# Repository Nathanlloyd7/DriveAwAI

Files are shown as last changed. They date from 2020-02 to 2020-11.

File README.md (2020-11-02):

# DriveAwAI - Final Year Project - Nathan Lloyd
Welcome to my Final Year Project as an undergraduate, the aim of this project is to have a semi autonomous vehicle that naturally has the ability to toggle between assisted. This will be done utilising a Pi 4, Coral TPU and explorerHAT Pro.

## Objectives
* Create a Raspberry Pi RC Car
* Provide a suitable GUI control
* Include autonomous driving elements, utilising computer vision
* Provide suitable security 

## Shopping List

Item | COST | Link
-----|------|-----
Raspberry Pi 4 | £30 - 50 | https://thepihut.com/products/raspberry-pi-4-model-b?variant=20064052740158
SD Card (Recommend 32GG+) | ?? | UP2U
ExplorerHat Pro | £20 | https://thepihut.com/products/explorer-hat
Coral TPU | £75| https://www.mouser.co.uk/ProductDetail/Coral/G950-01456-01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
PiCam V2 | £25 | https://thepihut.com/products/raspberry-pi-camera-module
PiCam Mount | £3 | https://shop.pimoroni.com/products/raspberry-pi-camera-mount
Extra Webcam | £? | https://www.amazon.co.uk/TeckNet%C2%AE-1080P-Webcam-Built-Microphone/dp/B003VOEENG
Motors & Wheels | £8 | 2 PCS DC Gear Motor + Tire Wheel for Arduino DC 3V-6V
Fan Shim | £10 | https://thepihut.com/products/fan-shim-for-raspberry-pi
Ninja Case | £8.50 | https://thepihut.com/products/pibow-4-coupe-case-for-raspberry-pi-4b?variant=20452597661758  
Dragging Wheel (Shooping Cart) | £3 | https://www.amazon.co.uk/gp/product/B007OXBMQM/ref=ppx_yo_dt_b_asin_title_o00_s00?ie=UTF8&psc=1
Jumper Wires M-M | £5 | https://www.amazon.co.uk/gp/product/B0144HG2RE/ref=ppx_yo_dt_b_asin_title_o01_s00?ie=UTF8&psc=1
LED's x2 | £2.50 | https://thepihut.com/products/adafruit-diffused-5mm-led-pack-5-leds-each-in-5-colors-25-pack-ada4203
Resistor x2 | £6 | https://thepihut.com/products/ultimate-resistor-kit
Blue Tape | £1 | https://www.amazon.co.uk/gp/product/B0001IXA76/ref=ppx_yo_dt_b_asin_title_o02_s00?ie=UTF8&psc=1
Pi Cam Ribbon Ext | £4 | https://www.amazon.co.uk/gp/product/B01MU2HAOM/ref=ppx_yo_dt_b_asin_title_o03_s00?ie=UTF8&psc=1
Toy Traffic Signs | £12 | https://www.amazon.co.uk/gp/product/B07PD2M9C4/ref=ppx_yo_dt_b_asin_title_o00_s00?ie=UTF8&psc=1
Battery Pack | TBD | TBD
Webcam  up2u | up2u
Total| £200 -£250 | I've not gone out to look for the best deal, so please do that yourself.

Some of the above aren't exactly what I bought and in some cases I had parts laying around from previous projects. This is just a guide to what you may need if you fully recreate. 

## Car Body
I have had a lot of help from a friend designing a chassis to fit the items I've accumilated, you can use whatever you want for your body... but the CAD models and designs will be displayed within a folder shortly.

## Extra Camera
As noted in my 2nd report, an Issue was running the Object detection model as well as onboard camera display using the same input. A simple workaround was using two cameras and mounting the second on top.

## Installing Coral TPU
Step 1: Install Coral TPU - https://coral.ai/docs/accelerator/get-started/

>echo "deb https://packages.cloud.google.com/apt coral-edgetpu-stable main" | sudo tee /etc/apt/sources.list.d/coral-edgetpu.list
>curl https://packages.cloud.google.com/apt/doc/apt-key.gpg | sudo apt-key add -
>sudo apt-get update

>sudo apt-get install libedgetpu1-std

Step 2: Install TF for Python - https://www.tensorflow.org/lite/guide/python
>pip3 install https://dl.google.com/coral/python/tflite_runtime-2.1.0.post1-cp37-cp37m-linux_armv7l.whl

Step 3: Check Installs by running a model
>mkdir coral && cd coral
>git clone https://github.com/google-coral/tflite.git

>cd tflite/python/examples/classification
>bash install_requirements.sh

>python3 classify_image.py \
>--model models/mobilenet_v2_1.0_224_inat_bird_quant_edgetpu.tflite \
>--labels models/inat_bird_labels.txt \
>--input images/parrot.jpg

# Installing Requirements
Step 1: <br/>
>Enable i2c, SSH, Camera and VNC  in Raspberry Pi config.<br/>

Step 2:<br/>
>Download the project if you haven't already.<br/>

Step 3:<br/>
>Unzip<br/>

Step 4:<br/>
>Navigate to the directory (/DriveAwAI-Nathanlloyd7) through terminal, here you can find the requirements doc. Then Run <br/>
>pip install --user --requirement Requirements.txt<br/>

Step 5: <br/>
>Run main: default password on SenseHat PIN password = 4321. Have fun with your new car

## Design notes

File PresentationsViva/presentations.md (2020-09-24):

# Why?
*I have decided to upload my viva presentations for safekeeping as access to the onedrive has been removed upon graduating.*

**Click Images to go to video**

## Video 1
* The problem
* The chassis
* The GUI

Video 1 (https://youtu.be/bGszfEqLIKk "Video 1 - Click to Watch!")

## Video 2
* Project Management, Issues & Flexibility 
* PIN Sytem Security
* Hashing PIN Password

Video 2 (https://youtu.be/l-lXbyoH-wU "Video 2 - Click to Watch!")

## Video 3
* Coral TPU
* What problem to tackle?
* The dataset & Transfer learning
* New Data & Processing
* Methodology 
* TensorFlow & Google Cloud
* TensorBoard
* Model analysis
* Implementation
* Future Improvements

Video 3 (https://youtu.be/PnvW7pgBxbs "Video 3 - Click to Watch!")

## Video 4
* Device Walkthrough

Video 4 (https://youtu.be/6IMir6JdNHE "Video 4 - Click to Watch!")

## Video 5
* Github
* Project Management Stategies
* Problems faced

Video 5 (https://youtu.be/kdOTbvWSUvU "Video 5 - Click to Watch!")

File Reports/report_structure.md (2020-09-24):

# Reports

*My dissertation project report is split into two segments due to the assessment structure.* 

## Part 1 
* Literature review
* Systems design and technical documentation
* The test plan 
* Current development timeline

## Part 2 
* Additional literature review discussing problems and objectives
* Development lifecycle
* Implemented and finished designs
* Core features
* Model development
* Model analysis 
* Critical analysis of tools and practices.

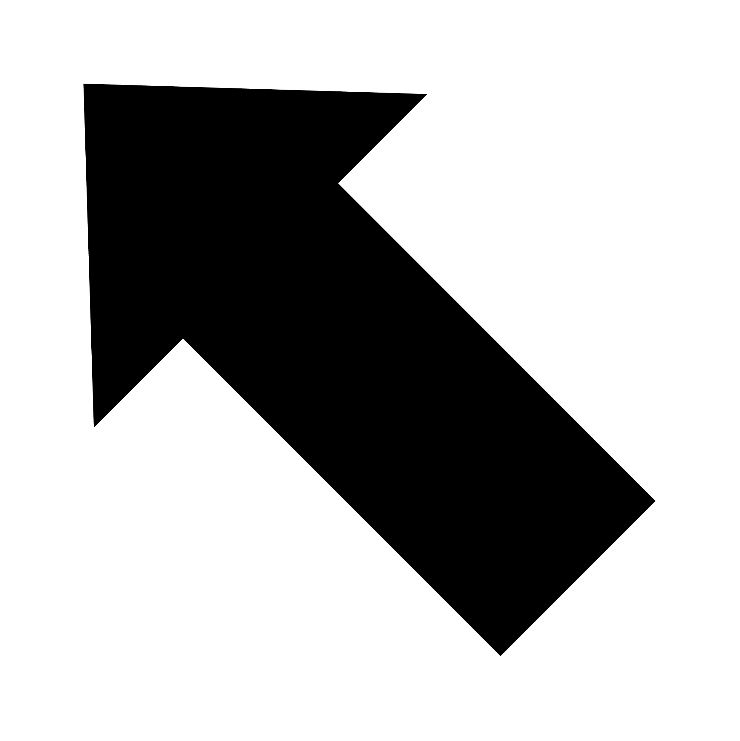
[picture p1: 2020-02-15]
Code/Images/Arrow-UL.png

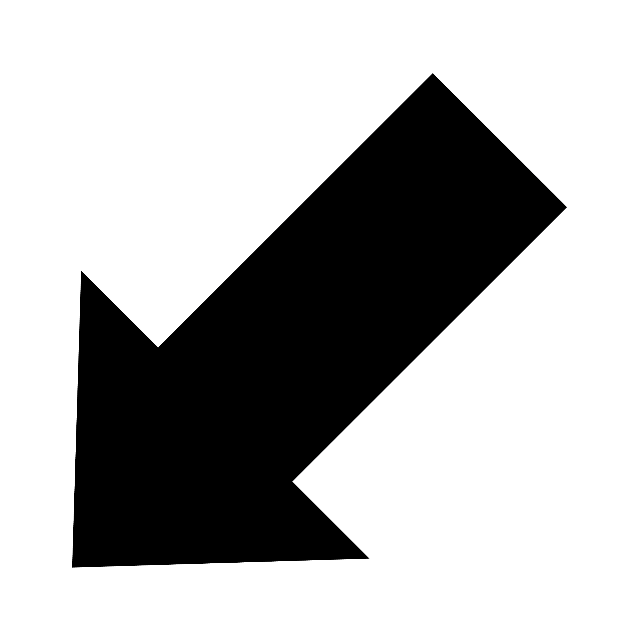
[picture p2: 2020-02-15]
Code/Images/Arrow-DL.png

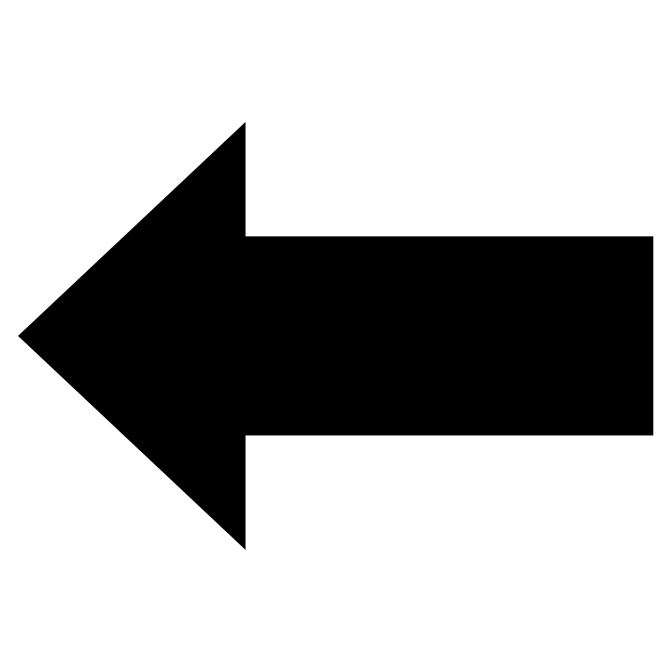
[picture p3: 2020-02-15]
Code/Images/Arrow-LE.png

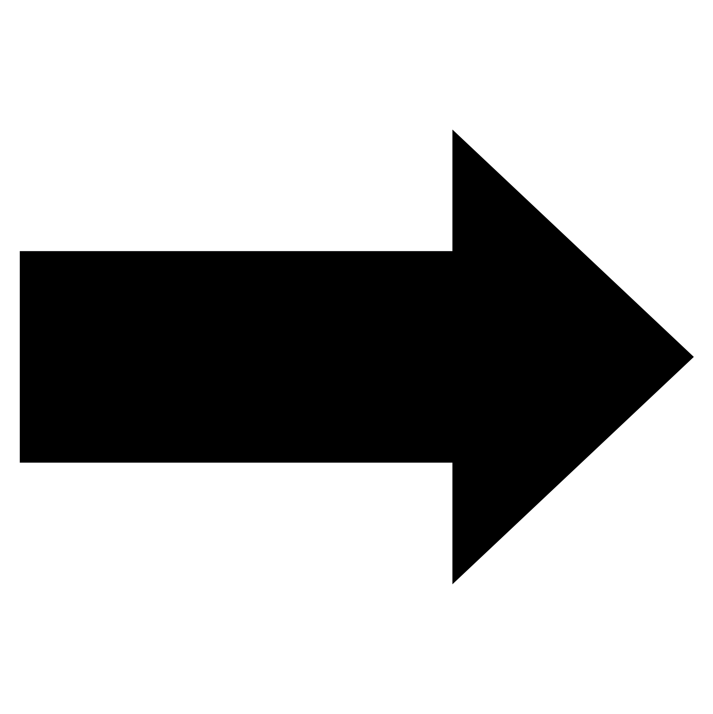
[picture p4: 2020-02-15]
Code/Images/Arrow-RI.png

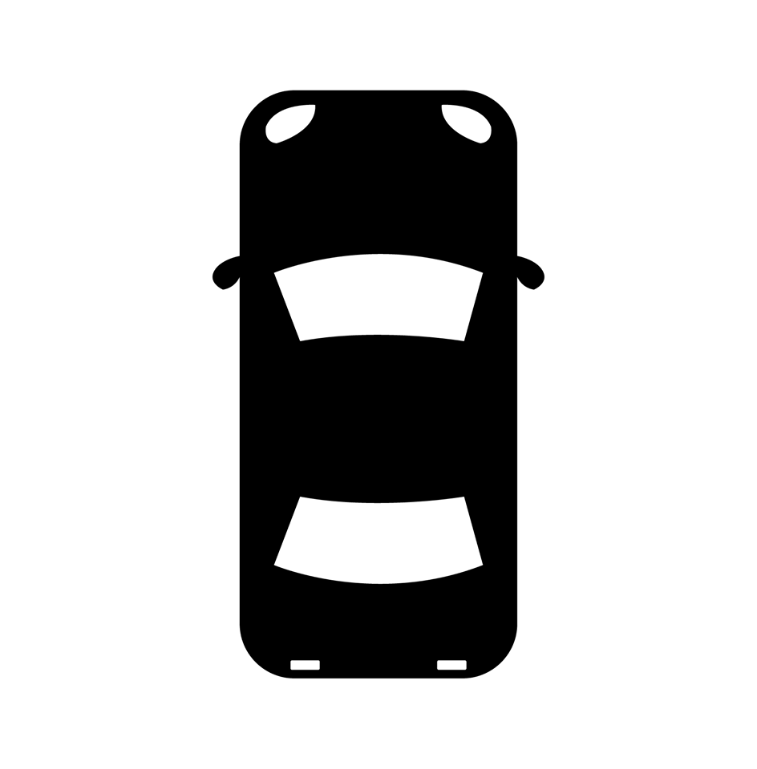
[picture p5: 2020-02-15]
Code/Images/realcar1.png

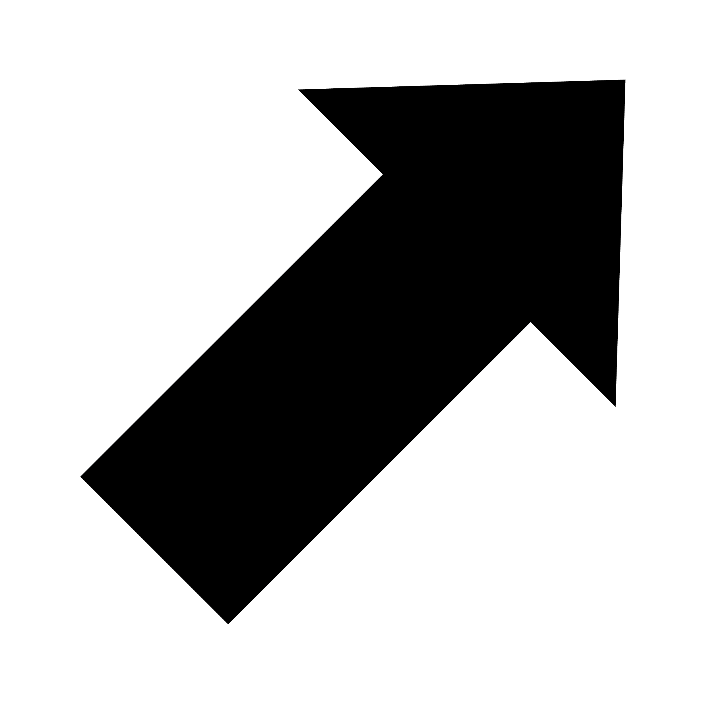
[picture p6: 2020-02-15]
Code/Images/Arrow-UR.png

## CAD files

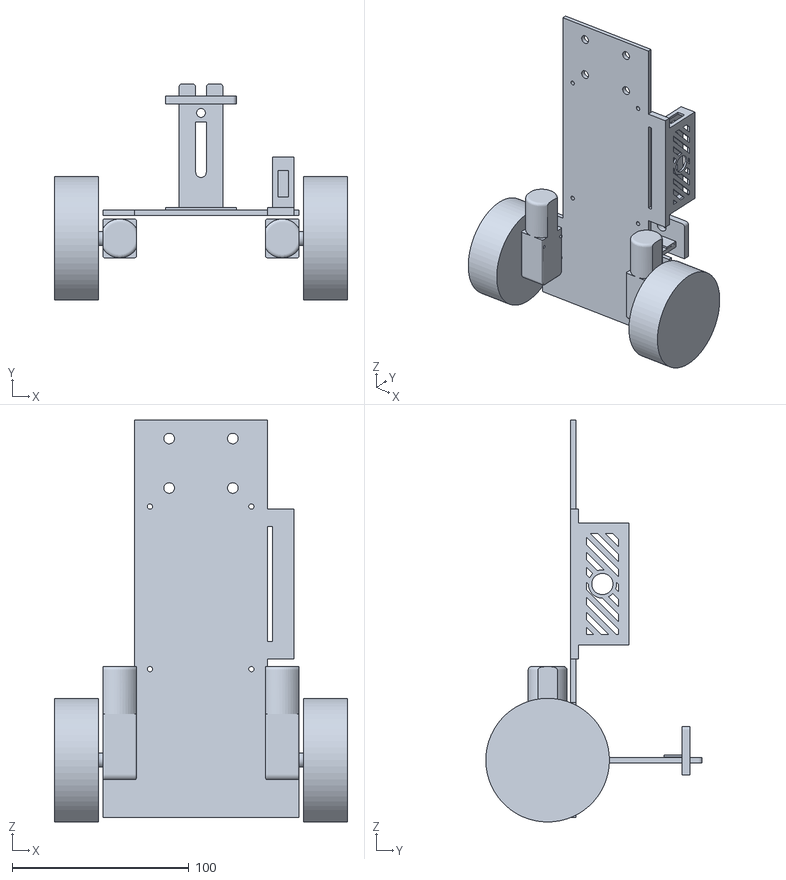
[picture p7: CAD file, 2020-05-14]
3D-Designs/FullModelWithoutMotorCasings.STL
166.0 x 122.5 x 227.5

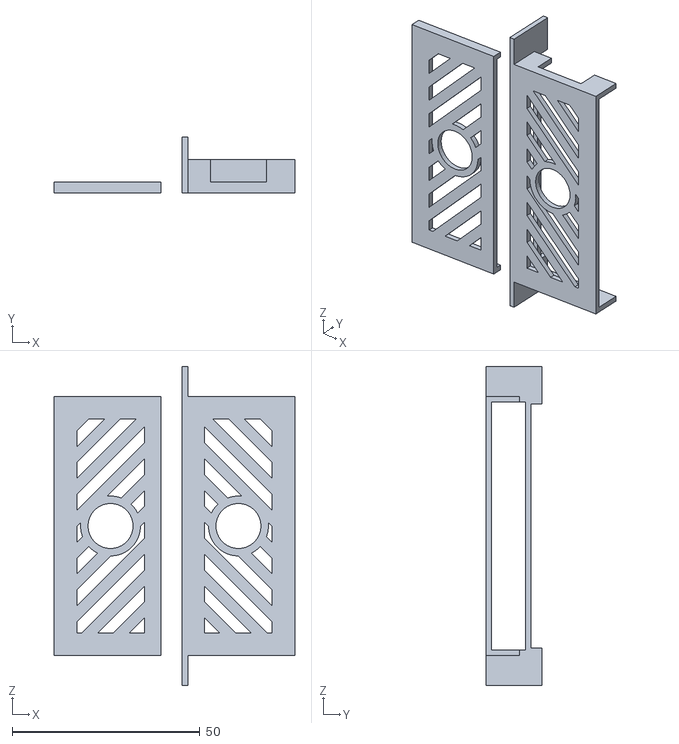
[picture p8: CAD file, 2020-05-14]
3D-Designs/CoralCase.STL
64.1 x 15.0 x 85.0

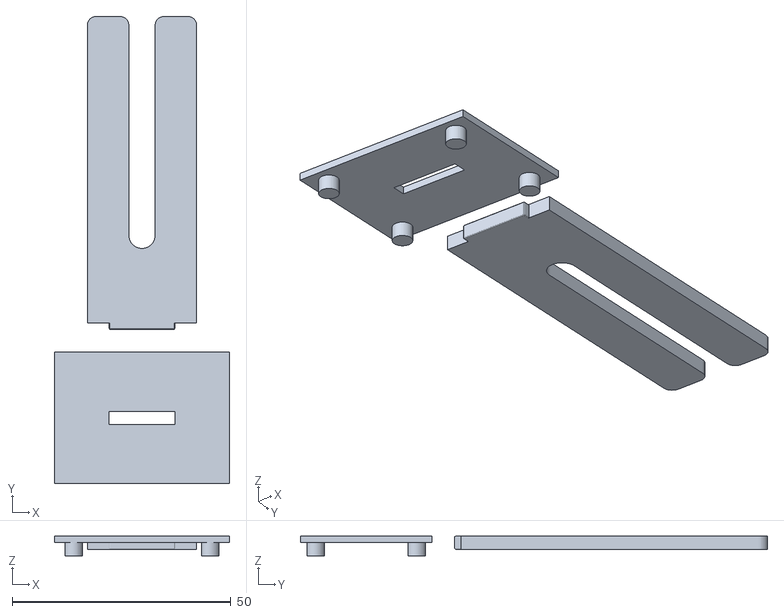
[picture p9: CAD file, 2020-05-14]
3D-Designs/CameraStand.STL
40.0 x 106.7 x 4.50

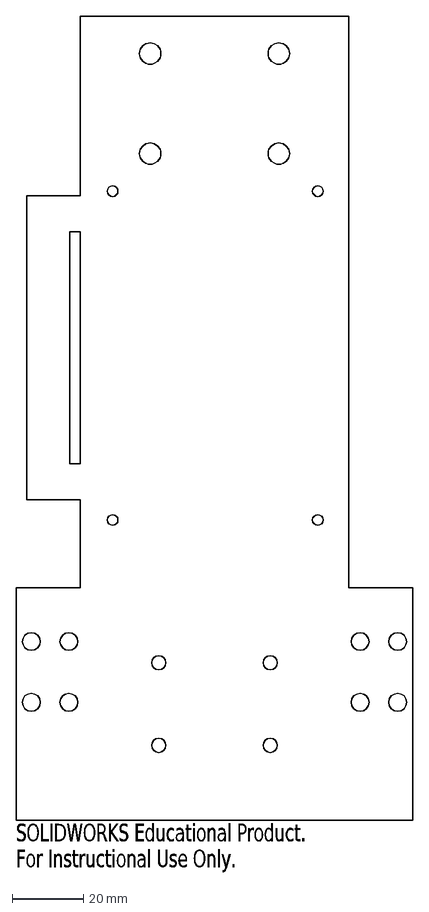
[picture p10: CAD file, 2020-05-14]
3D-Designs/BaseTemplateLaserCutting.DXF
SOLIDWORKS Educational Product.
For Instructional Use Only.

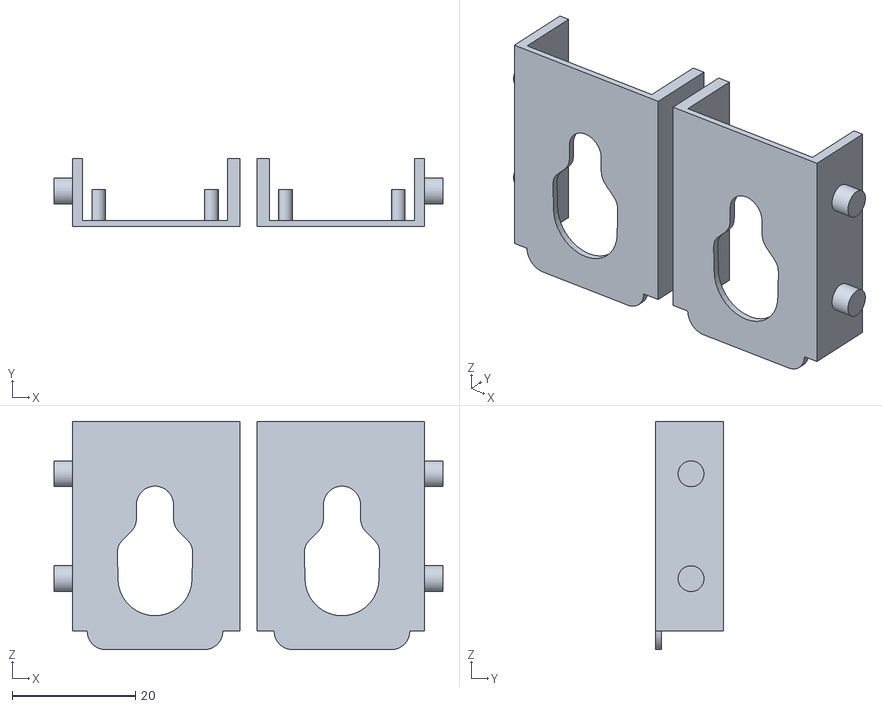
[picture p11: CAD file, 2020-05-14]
3D-Designs/MotorCasing.STL
63.0 x 11.0 x 37.0

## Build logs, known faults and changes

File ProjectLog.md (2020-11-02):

# DriveAwAI
Final Year Project

This is my dissertation project to create a rc car and develop it to have some level of automation using images. This will be used as a log/update for myself.

03.09.19
[Added in after the fact]
Assembled electronics and did some research into the cassis of the Pi car, looked into accelerators for increased calculation speed. Built some basic functions to do directions etc. Soldered wires to motors.

08.09.19
Building on previous basic motor control I've been working on some basic GUI's using tkinter. I've created three column panels: speed, directiom, video view. The latter of which is just a default panel seen on a tutorial, currently they do not interact with the motors as I ran out of time and couldn't upgrade to an RCCar Class. Future updates will include this, at the moment the buttons will just print their expected future feature. This is a very simple draft of the panels, more items may be added in future.
In the meantime of creating the gui and learning some basic tkinter I have started the fast.ai course which library sits on top of pytorch, this looks like a very efficient way of implementing ML. And with a coral TPU accelerator I think the overall goal will be very achievable.

12.09.19
Been busy over the last few days, not much programming or research taken place. I have put a few minutes in here and there to fix problems I was stuck on last week. I can now call methods when clicking a button which is the first GUI interaction I've achieved between motor and gui. I've also been pseduo coding a rc car class, and have put together a simple set motor implementation and it works fine, will just need to fit it with actual code and test it over the gui over the coming days. Done a little quote hunting collection and put them together for my lit review too. 
--Ext: After spending time of making a functional RC class, I've hit the problem I thought I may have by putting my speed and distance into seperate containers. when speed is updated, the direction panel has no idea. For this to be solved, do I simply need to use global variables or should I make new methods that send this info over? 

!!I think the best way forward would be to initialize my rc car in the RCTK window and have all my panels speak to this window.

19.09.19
Moved into Uni halls now, so potentially more frequent work. Merged the speed and direction panel into a movement panel. Adding diagonal turning too, currently the buttons don't match up in size, but eventually I will use images(arrows) to point in the direction. DIrections have not been coded in other than forward and backward as there is no chassis, so right and left is undecided. Added in a scale/slider for speed as it is more representative of real driving. Also added some basic menu buttons. Need to clean the code out and ideall would like to OOP up my menu buttons to make RCTK cleaner. But it is less important as these are secondary features. Still trying to find out how to access a stream of the picam too. Have some ideas but not seen any absolutes as of yet.

23.09.19
Added minor features to some of the menu items and changed about from a new window to a message box. I can see these menu items taking up a lot of room and it's not too clean coding having them in the RCTK file. Might need to implement OOP in the future to bring these menu items in. However I might save cleaning up my code until I have working up features as it is more important I get things working first.

27.09.19
Swapped to a pair of radio buttons for my one menu item. the menu saves and loads as expected but I can't display in the log box. I can sometimes get one working but not the other, could be an issue with the var or the r+/w+ access.

01.10.19
Created a new menu class to clean up RCTKWindow, I broke the save and load feature because of it but very happy with the cleaner approach. This approach as I followed a stack overflow posting meant I had to drop my root naming convention in RCTK in favour of initialising by tk.TK__init__(self) but other than those two issues fairly simple. Would be nice if I could get controller settings for a future update. Also realised I haven't posted the widget icon 'realcar1.png' but fairly straight forward so I wont post. Really happy with progress so far, think I'm going to go down an opencv & Tensor flow route so I can have an opencv stream in tkinter whereas currently getting the video in a frame is out of my knowledge.

04.10.19
Only small change today, got the save and load features working for the radio buttons on motor settings. Not as clean as I would like but it gets the job done. Next stage will be getting the loaded variables for the menu to actually interact with the panels

13.10.19
Videopanel added in, opencv needed for videostream as there is some complications when threading rpicam. Had a majority of the code done a few days ago but got stuck due to unfamiliarity with open cv syntax. Tried to use params where they weren't needed, but it is fixed now and working. Might look to add a menu that changes view by an open cv filter. "Night vision" Etc. Also looking to add "security features" where I can make use of the touch sensors on the explorer hat and make a password system.

16.10.19
Ran images for buttons through PhotoImage and they were too big and so couldn't resize, now using PIL library to edit them in app. Using images for buttons has slowed the start up slightly. Optimising this would be ideal. Changed the layout of code for rc and menu, initialising them both as self will allow me to use more features and have cleaner code.
----- I am definately keen on this password idea as well as some fun features like a horn.

21.10.19
Gone home for the week and so I haven't done any coding or research as I want some downtime, I have started to fill in a project contract however and decided to go from a scientific title to a more commerical one. I have decided to give the project an official name of 'Drive AwAI' which stands for "Drive Assisted with AI", I really like the title name and have enjoyed the downtime. I am looking forward to carrying on with the work at the end of this week. Hopefully I can add in a few fun features, the University has purchased a coral TPU on my behalf which is great. As I am already ahead of schedule, getting this device puts me even further ahead as it is the device I had in mind at the start of the project and now I do not need to replan or pay extra money to ensure I get it operational.

26.10.19
Quick little security password for my RC, thought I might as well use the touch sensors on the explorerhat as they make a great PIN entry system. Found a majority of this programming online but added the ability to change the password, next step will be saving and loading a password in. Might add it into my settings folder but I'm not sure how without deleting other settings. Works fine, just need to clean up the looping system and find out how to attach to the rest of the app, it is low priority at the moment though. Got the Coral TPU this week too, so I can start earlier than planned on ML.

10.11.19
With other deadlines looming way before this one, and already being a decent way through the development of the front end of this app I've taken my foot off the gas and will continue to do so for another week I expect. I have been making a list and updating my development timeline accordingly though. I did get a bit bored though and wanted to get the password system in place, I've made the password load in from a txt file called, passSeting.txt, and then split the string and cast so they can be formatted into a list. This means I can simply enter a string when I edit the change password setting and not have any complicated stuff. I did try and get the TPU on, but as I already had a previous install of tf and a workaround method for 3.5 python. It would seem as they now support 3.7 there is a clash, will have to uninstall libraries or reformat the SD and reinstall from scratch.

15.02.20
Long time since the last log, bogged down with other uni work but I have been working on this as some commits show. I have a model working with the TPU but it currently doesn't effect the Pi, it can see but not act upon anything. I have also been working on the chassis and its nearly complete. Because of this I can add directional functionality... however, it may need fine tuning. I have spent some of the day just cleaning up the files, I want be able to curl in my files between different SD cards and have everything pre-installed by doing so. So a bit of housekeeping is going to occur to do this.

17.02.20
Have created requirements file.
Have also added extra security by hashing the pin passwords.**Hash of these commits matches 4321, however, github adds whitespace at the end of the line, so please remove this**

03.03.20
Removed flip from the video stream. 
Spent the last week finishing up the core driving elements, motors are now installed using 3D printed elements, car can now be driven using GUI. Need to shift the minimum speed selectable though in slider. 35 is too slow. 50 is new minimum.

Also bought toy model traffic signs, taken 120 photos containing around 250 object instances. Used LabelImg to box the signs and toy person. Got a few left to do as I need to retake a few photos due to poor image quality. After this I can xml -> CSV -> TFRecord ... and then start training (transfer learning on MobileNet v2 SSD COCO), COCO contains a few objects that I could use anyway, such as cars, people, trucks et. MobileNet v2 SSD is well documented and middleground of accuracy and speed. May try and train my own from scratch not using COCO but will see.

11.05.20
It has been a very long time since I have used the log. I will give a very short but sweet update on what I've been working on.
- Chassis is virtually done
- There are loads more photos and objects within each photo
- Three models were created, expanding dataset each time
- 3rd Model, although could be improved further is suitable
- Coral TPU is a pain to work with 'libedgetpu.so.1' is the bain of my existence
- I can get the model to work outside of the application and control motors seperately
- GUI barebones is done.

Project is nearly at the end for what I set out to do. I have a week left to try and wrestle the edgetpu into submission, otherwise I have a tech demo for the model controlling motors and a seperate one for the GUI/Security/Car. Bit of a pain to have everything done but the last segments not wanting to co-operate.

02.11.20
Bit late on the total project update, I graduated CompSci with a first and got 98% in my dissertation project overall. Managed to wrangle the last bit of the project together and everything worked as expected in the end; see my presentations and reports that were uploaded previously. I am just revisting this project now as I wanted to have a bit of closure on the last whitespace "feature" of the hashed password (all it took was an rstrip). Overall this has been a very fun project and has introduced me to loads of cool AI/Deep Learning content. I'm continuing my studies in a masters, hopefully upskilling from implementing others NN's in transfer learning to making my own from scatch :D.

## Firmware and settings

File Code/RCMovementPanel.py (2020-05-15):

#control direction of rc
from tkinter import *
from Code.RCCar import *
from PIL import Image, ImageTk
import os
import Code.RCAutomated as rcauto


class RCMovementPanel:
    def __init__(self, root, frame):
        self.rc = RCCar(True, 50, 50)
        self.root = root
        self.frame = frame
        dlpath = os.getcwd()
        motorSetsFile = open(dlpath+"/Code/Settings/motorSetting.txt", "r") #current setup lets you save to a doc but not show in a log or print in??
        global loadedVar
        loadedVar = motorSetsFile.read(1)
        
            
            
        
        
        
#images import and process into smaller size
        try:
            self.arrowSy = 50   #customizable maybe a menu item?
            self.arrowSx = 50
            self.arrowUp = Image.open(dlpath+"/Code/Images/Arrow-UP.png")
            self.arrowUp = self.arrowUp.resize((self.arrowSx,self.arrowSy), Image.ANTIALIAS)
            self.arrowUp = ImageTk.PhotoImage(self.arrowUp)

            self.arrowUr = Image.open(dlpath+"/Code/Images/Arrow-UR.png")
            self.arrowUr = self.arrowUr.resize((self.arrowSx,self.arrowSy), Image.ANTIALIAS)
            self.arrowUr = ImageTk.PhotoImage(self.arrowUr)

            self.arrowUl = Image.open(dlpath+"/Code/Images/Arrow-UL.png")
            self.arrowUl = self.arrowUl.resize((self.arrowSx,self.arrowSy), Image.ANTIALIAS)
            self.arrowUl = ImageTk.PhotoImage(self.arrowUl)

            self.arrowRi = Image.open(dlpath+"/Code/Images/Arrow-RI.png")
            self.arrowRi = self.arrowRi.resize((self.arrowSx,self.arrowSy), Image.ANTIALIAS)
            self.arrowRi = ImageTk.PhotoImage(self.arrowRi)

            self.arrowLe = Image.open(dlpath+"/Code/Images/Arrow-LE.png")
            self.arrowLe = self.arrowLe.resize((self.arrowSx,self.arrowSy), Image.ANTIALIAS)
            self.arrowLe = ImageTk.PhotoImage(self.arrowLe)

            self.arrowDl = Image.open(dlpath+"/Code/Images/Arrow-DL.png")
            self.arrowDl = self.arrowDl.resize((self.arrowSx,self.arrowSy), Image.ANTIALIAS)
            self.arrowDl = ImageTk.PhotoImage(self.arrowDl)

            self.arrowDo = Image.open(dlpath+"/Code/Images/Arrow-DO.png")
            self.arrowDo = self.arrowDo.resize((self.arrowSx,self.arrowSy), Image.ANTIALIAS)
            self.arrowDo = ImageTk.PhotoImage(self.arrowDo)

            self.arrowDr = Image.open(dlpath+"/Code/Images/Arrow-DR.png")
            self.arrowDr = self.arrowDr.resize((self.arrowSx,self.arrowSy), Image.ANTIALIAS)
            self.arrowDr = ImageTk.PhotoImage(self.arrowDr)

        except:
            print("Something went wrong, File not found")




#Frame for Directional Buttons & speed
        Label(self.frame, text="Direction:").grid(row=0, column=0, padx=10, pady=2)

#top row
        self.topFrame = Frame(self.frame, width=200, height=10, borderwidth=1)
        self.topFrame.grid(row=1, column=0, padx=10, pady=2)
        self.left_upBtn = Button(self.topFrame, text="diag", image=self.arrowUl, command= self.rc.goUpLeft)
        self.left_upBtn.grid(row=1, column=1, padx=10, pady=2)
        self.upBtn = Button(self.topFrame, text="Up",image=self.arrowUp, command= self.rc.goForward)
        self.upBtn.grid(row=1, column=2, padx=10, pady=2)
        self.right_upBtn = Button(self.topFrame, text="diag", image= self.arrowUr, command= self.rc.goUpRight)
        self.right_upBtn.grid(row=1, column=3, padx=10, pady=2)
#Frame to Hold left, stop and right
        self.midFrame = Frame(self.frame, width=200, height=10, borderwidth=1)
        self.midFrame.grid(row=2, column=0, padx=10, pady=2)
        self.leftBtn = Button(self.midFrame, text="Left",image = self.arrowLe, command=self.rc.goLeft)
        self.leftBtn.grid(row=0, column=0, padx=10, pady=2)
        self.stopBtn = Button(self.midFrame, text="Stop", command = self.rc.handbreak)
        self.stopBtn.grid(row=0, column=1, padx=10, pady=2)
        self.rightBtn = Button(self.midFrame, text="Right",image = self.arrowRi, command =self.rc.goRight)
        self.rightBtn.grid(row=0, column=2, padx=10, pady=2)
#Down
        self.botFrame = Frame(self.frame, width=200, height=10, borderwidth=1)
        self.botFrame.grid(row=3, column=0, padx=10, pady=2)
        self.left_downBtn = Button(self.botFrame, text="Diag",image=self.arrowDl, command= self.rc.goBackLeft)
        self.left_downBtn.grid(row=0, column=1, padx=10, pady=2)
        self.downBtn = Button(self.botFrame, text="Down",image=self.arrowDo, command= self.rc.goBack)
        self.downBtn.grid(row=0, column=2, padx=10, pady=2)
        self.right_downBtn = Button(self.botFrame, text="Diag", image=self.arrowDr,command= self.rc.goBackRight)
        self.right_downBtn.grid(row=0, column=3, padx=10, pady=2)
        Label(self.frame, text=" ").grid(row=4, column=0, padx=10, pady=2)
#Auto/Man Toggle
        
        self.aiTogBtn = Button(self.frame, text="Ai Toggle", command=rcauto.goAI)
        self.aiTogBtn.grid(row=5, column=0, padx=10, pady=2)
#speed
        global scale
        Label(self.frame, text=" ").grid(row=6, column=0, padx=10, pady=2)
        self.speedFrame = Frame(self.frame, width=200, height=10, borderwidth=1)
        self.speedFrame.grid(row=7, column=0, padx=10, pady=2)
        Label(self.speedFrame, text="Speed:").grid(row=0, column=0, padx=10, pady=2)
        self.scale = Scale(self.speedFrame, from_ = 35, to = 100, orient = HORIZONTAL)
        self.scale.grid(row=1, column=0, padx=10, pady=2)
        self.scale.set(75)                                                                           #sets default speed
        self.setSpeed = Button(self.speedFrame, text="Set Speed", command = self.returnSpeed)
        self.setSpeed.grid(row=2, column =0, padx=10, pady=2)
            
    def returnSpeed(self):
        if int(loadedVar) == 1:
            self.rc.set__spd(self.scale.get())
            print (self.scale.get())     #mock function for now
        elif int(loadedVar) == 0:
            messagebox.showwarning(title="Modification = Off", message = "This safety feature has been toggled.\nPlease go to Motor settings to remedy this!")
            print("control off")
        else:
            print('An error occurred trying to analyse file contents')
     
       
    def speedOff(self):
           setSpeed.configure(state="disabled")
           scale.config(state=DISABLED)
           

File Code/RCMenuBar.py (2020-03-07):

import tkinter as tk
from tkinter import *
from tkinter import messagebox
import sys
import os

class RCMenuBar(tk.Menu):
    def __init__(self, parent):
        tk.Menu.__init__(self, parent)
        dlpath = os.getcwd()
        fileMenu = tk.Menu(self, tearoff=0)
        self.add_cascade(label="File",underline=0, menu=fileMenu)
        fileMenu.add_command(label="Control Settings",underline=0, command = self.controlSetting)
        fileMenu.add_command(label="Motor Settings",underline=0, command = self.motorSetting)
        fileMenu.add_command(label="Password Settings",underline=0, command = self.passSetting)
        fileMenu.add_command(label="Fun Settings",underline=0, command = self.funSetting)
        fileMenu.add_separator()
        fileMenu.add_command(label="Exit", underline=1, command= quit)
        helpMenu = tk.Menu(self, tearoff=0)
        self.add_cascade(label="Help", menu = helpMenu, underline=0)
        helpMenu.add_command(label="About", underline=0, command = self.about)
        #keyboard shortcuts
        self.bind_all("<Control-a>", self.about)
        self.bind_all("<Control-c>", self.controlSetting)
        self.bind_all("<Control-m>", self.motorSetting)



# ------------------------ About Menu Item ------------------------
    def about(self):
        messagebox.showinfo("About", """Hello, welcome to this RC application\n
        This application will function as a minature version of a real full size car, giving the user the ability to control it using GUI or keyboard inputs as well as toggle assistive driving technologies:\n
        If you have any questions please contact N Lloyd here:\n P16187037@my365.dmu.ac.uk""")

# ------------------------ Vehicle Control Menu Item's and Methods ------------------------
    def controlSetting(self):  #will allow customization
        controlSet = Toplevel()
        controlSet.title("Control Panel")
        controlSet.minsize(300,300)
        Label(controlSet, text="This is the Control Page\n Here you can switch between kyboard, UI, controller perhaps").grid(row=0, column=1, padx=10, pady=2)
        controlSet.mainloop()


# ------------------------ Password Change Menu Item's and Methods ------------------------

    def passSetting(self):  #will allow customization
        global passSet #so it can be destroyed
        passSet = Toplevel()
        passSet.title("Password Panel")
        passSet.minsize(300,300)
        dlpath = os.getcwd()
        passSetsFile = open(dlpath+"/Code/Settings/passSetting.txt", "r")
        loadedPass = passSetsFile.readline()
        passSettingFrame = Frame(passSet, width=200, height=10, borderwidth=1)
        passSettingFrame.grid(row=1, column=0, padx=10, pady=2)
        Label(passSet, text="This is the password Page\n here you can change password settins and logon").grid(row=0, column=0, padx=10, pady=2)
        pwNum1 = Button(passSettingFrame, text="1", command = lambda : self.addtoPW(1)).grid(row=0, column=0, padx=10, pady=2)
        pwNum2 = Button(passSettingFrame, text="2", command = lambda : self.addtoPW(2)).grid(row=0, column=1, padx=10, pady=2)
        pwNum3 = Button(passSettingFrame, text="3", command = lambda : self.addtoPW(3)).grid(row=0, column=2, padx=10, pady=2)
        pwNum4 = Button(passSettingFrame, text="4", command = lambda : self.addtoPW(4)).grid(row=0, column=3, padx=10, pady=2)
        global newPWLog
        newPWLog = Text(passSet, width = 20, height = 2, takefocus=0, state="disabled")
        newPWLog.grid(row=4, column=0, padx=10, pady=2)
        #newPWLog.insert(0.0,"Enter Password: ")
        Label(passSet, text="Enter Password").grid(row=3, column=0, padx=10, pady=2)
        passSetFinal = Frame(passSet, width=200, height=10, borderwidth=1)
        passSetFinal.grid(row=5, column=0, padx=10, pady=2)
        clearPW = Button(passSetFinal, text="Clear", command = self.clearPW).grid(row=0, column=0, padx=10, pady=2)
        submitPW = Button(passSetFinal, text="Submit", command = self.savePass).grid(row=0, column=1, padx=10, pady=2)

        passSetsFile.close()
        passSet.mainloop()


    def savePass(self):
        import bcrypt
        dlpath = os.getcwd()
        passSetsFile = open(dlpath+"/Code/Settings/passSetting.txt", "wb")
        newPin = newPWLog.get(0.0,'end-1c')
        if len(str(newPin)) == 4: #edit this to change pw length
            listPin = []
            for c in newPin: #appends each textbox element to a list, list format required for pin
                listPin.append(int(c)) #converts to int to remove 'x' format
            
            hashed = bcrypt.hashpw(str(listPin).encode("utf-8"), bcrypt.gensalt()) #encode and salt
            passSetsFile.write(hashed)
            passSetsFile.close()
            passSet.destroy()
        else:
            messagebox.showwarning(title="Invalid Password", message = "Must have 4 digits!")

    def addtoPW(self, pwNum):
        newPWLog.configure(state="normal")
        newPWLog.insert(END, pwNum)
        newPWLog.configure(state="disabled")
        
    def clearPW(self):
        newPWLog.configure(state="normal")
        newPWLog.delete(0.0,END)
        newPWLog.configure(state="disabled")







# ------------------------ Fun Settings Menu Item's and Methods ------------------------
    def funSetting(self):  #will allow customization
        funSet = Toplevel()
        funSet.title("Control Panel")
        funSet.minsize(300,300)
        Label(funSet, text="This is the Fun Page\n here you can change fun effects for the vehicle").grid(row=0, column=1, padx=10, pady=2)
        funSet.mainloop()
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

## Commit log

2019-09-01 Create Basics v0.01
    Just a quick tech demo of explorerhat to test features. Will need to add L & R turning when chassis is built. Also add in wireless keyboard feature for now, later can be controlled over vnc, later no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
2019-09-02 Update and rename Basics v0.01 to Basics v0.02
    fSoldered both motors to their respective jumper cables. Cleaned up the code for future use by using methods.
2019-09-12 Update RCSpeedPanel.py
    RC speed panel, figured out how to use methods on a button command, overlooked the fact I did not need to call it with brackets.
    Updating speed as shown here was just to test this, as updating like this for the full app would just trigger the motors rather than update a speed variable. Currently working on RC class, just getting set speed functions to fix this problem
2019-09-12 Update RCDirectionPanel.py
    This command works with the new RCClass added. However because the panels are in their own classes the motor speed variables do no communicate with one-another and so when the speed is set in the speed panel it is not picked up by the directional panel. Whether this can be solved by changing var's too global or whether I need to rejig some methods, I'm not sure.
2019-09-12 Update README.md
    update post rc class, including current problem
2019-09-19 Create RCMovementPanel
    Moved speed and Direction together for one Movement panel, changed out the buttons for a slider/scale feature. (Much more realistic for actual cars to move between speeds)
2019-09-19 Update RCCar
    Added a few new features, not done left/riight and diagonals yet as I don't have a chassis to fit motors too and fine tune.
2019-09-23 Update RCTKWindow.py
    Changed menu items a little, added some features to motor control. Changed the panel to a message box for about menu item too.
2019-09-27 Update RCTKWindow.py
    Added an icon, changed the buttons on the one half done setting. it now has a file it can save to. however it doesn't load in the var to show on the log??
    [RCTKWindow.py]
2019-10-26 RCPassword
    Quick little security password for my RC, thought I might as well use the touch sensors on the explorerhat as they make a great PIN entry system. Found a majority of this programming online but added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
2019-11-10 Update RCTKWindow.py
    Just added the RCPassword class, it loads from a file not attached, will need to make sure I put a feature to make sure this file is there in the future.
2020-02-15 Create motorSetting.txt
    Added motor setting placeholder file, these will be condensed into one file eventually
2020-02-17 Update RCMenuBar.py
    Needed to add a new list for the pin as the pin entry system takes a list in too, for loop appends the textbox characters as ints to remove ' ' formatting.
2020-03-03 Update RCVideoPanel.py
    Removed the flip (left to right mirror)
    [RCVideoPanel.py]
2020-03-08 Add files via upload
    Adding labelled training and testing data and subsequent xml files.
    90:10 split
    268 Total Objects over 120 Images
    Person: 60
    Traffic_Sign_30: 52
    Traffic_Sign_50: 52
    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
    [testing.csv, training.csv]
2020-05-14 Add files via upload
    Added files for the 3d designs used to build the chassis and supporting components.
    [BaseTemplateLaserCutting.DXF, CameraStand.STL, CoralCase.STL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]
2020-05-15 Update RCVideoPanel.py
    Edited code to deal with co processing of camera. Added a webcame as well as picam to avert the issue entirely.
    Change cv2.videocapture(1)/(0)
    [RCVideoPanel.py]
2020-05-15 Update RCMovementPanel.py
    added call of goAI method for ai toggle button
2020-05-15 Add files via upload
    Modified File from Evan Juras, used to run object detection through open, modified to control motors and open in new window when run in gui
2020-09-24 Reports/
    My dissertation project report is split into two segments due to the assessment structure.
    Part 1 contains: Literature review, systems design and technical documentation, the test plan and current position in development timeline.
    Part 2 contains: Additional literature review discussing objectives, development lifecycle, finished designs, core features, model development, model analysis and critical analysis of tools and pract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
